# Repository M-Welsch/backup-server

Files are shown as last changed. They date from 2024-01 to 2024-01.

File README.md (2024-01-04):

# Backup Server (BaSe)

Your Home NAS requires you to make backups from time to time. Since you have better things to do, these will likely get forgotten or done irregulary. The Backup-Server aims on helping you out. It backs up your data on schedule and undocks the backup medium when the backup is done. This offers an unique way of data protection.

## Introduction (longer)

Like many other people (*cough* nerds) I have a home NAS that serves nextcloud and some other funny stuff. Thanks to a terrific community it became quite easy to setup such a thing. Many, many thanks to you all!
However, hosting my own server came with a serious disadvantage. I had to take care of the backups myself.

I built Backup Server to overcome this issue. It sleeps and therefore consumes very, very little current most of the times, wakes up when a backup is scheduled, docks to a hard drive, copys all the data from the nas, undocks and goes back to sleep.



## Implementation

The current verion is built around a banana pi mk1. It connects to the hard drive via a motor-driven pluggable sata-connection, which is the core of the whole thing. This way, the harddrive is only connected to anything if needed.

```mermaid
graph LR
A(Power Up)-->B(Dock external HDD)-->C(Conduct Backup)-->D(Schedule Next Backup)-->E(Undock external HDD)-->F(Schedule next Backup)-->G(Power Down)
```

# Components

the next hardware version shall be more flexible compared to our custom fit to the banana pi.
# base-pcu

This has the directories

- ChibiOS
- ChibiOS-Contrib

as submodules.

```shell
git submodule add git@github.com:ChibiOS/ChibiOS.git
git submodule add git@github.com:ChibiOS/ChibiOS-Contrib.git
```

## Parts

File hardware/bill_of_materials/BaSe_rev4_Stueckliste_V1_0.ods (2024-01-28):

Stückliste BaSe HW rev4
Stand: 01/28/2024
Position | Bezeichnung | Menge | Einzelpreis | Gesamtpreis | Link
100 | Raspberry Pi 4 (oder kompatibler SBC) | 1 |  | 0,00 €
200 | BaSe_PWR_V4_0 Leiterplatte | 1 | 1,63 € | 1,63 €
201 | BaSe_PWR_V4_0 Bauteile | 1 | 40,83 € | 40,83 € | 35,47 € bei 25 Stück
210 | BaSe_HMI_V1_1 Leiterplatte | 0.2 | 6,30 € | 1,26 €
211 | BaSe_HMI_V1_1 Bauteile | 1 | 4,77 € | 4,77 € | 3,67 € bei 25 Stück, 2,93€ bei 100 Stück
212 | Display Modul | 0.2 | 10,49 € | 2,10 € | https://www.amazon.de/AZDelivery-HD44780-Display-Zeichen-Arduino/dp/B08216LXVQ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
220 | BaSe_USB_Adapter_Carriage_V1_0 Leiterplatte | 1 | 0,47 € | 0,47 €
221 | BaSe_USB_Adapter_Carriage_V1_0 Bauteile | 1 |  | 0,00 € | Preis in BaSe_PWR_4_0 enthalten
230 | BaSe_USB_Adapter_Frame_V1_0 Leiterplatte | 1 | 1,63 € | 1,63 €
231 | BaSe_USB_Adapter_Frame_V1_0 Bauteile | 1 |  | 0,00 € | Preis in BaSe_PWR_4_0 enthalten
300 | BaSe_hw4_frame_v2.stl | 1 |  | 0,00 €
301 | BaSe_hw4_carriage_v1.stl | 1 |  | 0,00 €
303 | USB 2.0 A auf Micro USB | 1 |  | 0,00 €
304 | USB 3.0 A auf Micro USB 3.0 | 1 | 6,05 € | 6,05 € | https://www.ebay.de/itm/145108187455
305 | Kugellager 608 ZZ 8x22x7mm Miniaturkugellager | 2 |  | 0,00 €
400 | Mikro Getriebemotor N20 12V 60rpm | 1 |  | 0,00 € | https://www.ebay.de/itm/384457943327
401 | Gewindekupplungen | 0.2 | 7,99 € | 1,60 € | https://www.amazon.de/YOTINO-Wellenkupplungen-Schrittmotor-Koppler-Aluminiumlegierung-Gelenkverbinder/dp/B07D9JWNFC
402 | Gewindestange (10cm) + Gewindemutter | 0.2 | 13,69 € | 2,74 € | https://www.amazon.de/Mavis-Laven-Gewindestange-Trapezgewindestange-Messingmutter-300mm/dp/B07SK6YZCM
 |  |  | Summe | 63,06 €

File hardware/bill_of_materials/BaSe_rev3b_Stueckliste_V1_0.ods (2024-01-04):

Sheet: Einkaufsliste
Stückliste BaSe HW rev3b
Stand: 30.08.2020
Position | Bezeichnung | Menge | Einzelpreis | Gesamtpreis | Link
100 | BananaPi Mk1 | 1 | 38,01 € | 38,01 € | https://www.conrad.de/de/p/banana-pi-bpi-m1-banana-pi-bpi-m1-1-gb-2-x-1-0-ghz-1196100.html
200 | BaSe_PWR_V3_2 Leiterplatte | 0,2 | 11,30 € | 2,26 €
201 | BaSe_PWR_V3_2 Bauteile | 1 | 45,79 € | 45,79 € | 35,47 € bei 25 Stück
202 | Schrittmotor Treibermodul | 0,2 | 7,99 € | 1,60 € | https://www.amazon.de/ARCELI-kompatibles-Stepper-StepStick-Motortauchermodul-K%C3%BChlk%C3%B6rper-3D-Drucker-Controller-Rampen/dp/B07MY2SWQ5
203 | Micro-USB Stecker | 0,05 | 9,39 € | 0,47 € | https://www.amazon.de/gp/product/B013FJKC28/ref=ppx_yo_dt_b_asin_title_o04_s00?ie=UTF8
210 | BaSe_HMI_V1_1 Leiterplatte | 0,2 | 6,30 € | 1,26 €
211 | BaSe_HMI_V1_1 Bauteile | 1 | 4,77 € | 4,77 € | 3,67 € bei 25 Stück, 2,93€ bei 100 Stück
212 | Display Modul | 0,2 | 10,49 € | 2,10 € | https://www.amazon.de/AZDelivery-HD44780-Display-Zeichen-Arduino/dp/B08216LXVQ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
220 | BaSe_SATA_Adapter_Carriage_V1_1 Leiterplatte | 0,2 | 3,00 € | 0,60 €
221 | BaSe_SATA_Adapter_Carriage_V1_1 Bauteile | 1 | 5,89 € | 5,89 € | 5,61 € bei 25 Stück, 4,60 € bei 100 Stück
230 | BaSe_SATA_Adapter_HDD_V1_1 Leiterplatte | 0,2 | 5,00 € | 1,00 €
231 | BaSe_SATA_Adapter_HDD_V1_1 Bauteile | 1 | 10,39 € | 10,39 € | 9,07 € bei 25 Stück, 8,22 € bei 100 Stück
300 | BaSe_Auflager_Platinen_rev3.stl
301 | BaSe_Bodenplatte_rev3.stl
302 | BaSe_BP_HDD_rev1.stl
303 | BaSe_HMI_Display_Abstandsrahmen_rev1.stl
304 | BaSe_rev1_Spannlager_Gegenstueck_2020_07_19.stl
305 | BaSe_Schlitten_rev3_2020_07_19.stl
400 | Schrittmotor: Nema 17 | 1 | 7,99 € | 7,99 € | https://www.ebay.de/itm/Schrittmotor-Nema-17-Stepper-Motor-32Ncm-1-2A-42x34mm-4-wire-1m-Cable-3D-Drucker/392587286914
401 | Gewindekupplungen | 0,2 | 7,99 € | 1,60 € | https://www.amazon.de/YOTINO-Wellenkupplungen-Schrittmotor-Koppler-Aluminiumlegierung-Gelenkverbinder/dp/B07D9JWNFC
402 | Gewindestange (10cm) | 0,2 | 13,69 € | 2,74 € | https://www.amazon.de/Mavis-Laven-Gewindestange-Trapezgewindestange-Messingmutter-300mm/dp/B07SK6YZCM
403 | Linearführung + Gleitlager + Spannbacken | 0,5 | 13,49 € | 6,75 € | https://www.ebay.de/itm/2-X-400mm-8mm-Linearfuhrung-Gleitschiene-Welle-4-X-SBR20UU-Linearblock/373092586135
404 | Endschalter (KW4-3Z-3 Schnappsch gs) | 0,4 | 4,09 € | 1,64 € | https://www.ebay.de/itm/5pcs-Mikro-Endschalter-lange-Hebel-Arm-Subminiatur-KW4-3Z-3-Schnappsch-gs/163894137501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
 |  |  | Summe | 134,84 €

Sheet: BaSe_PWR_V3_2_Stueckliste
Refs | Value | Footprint | Quantity | MFR | MPN | SPR | SPN
C1;C16;C6;C7 | 100nF | Capacitor_SMD:C_0603_1608Metric_Pad1.05x0.95mm_HandSolder | 4 | - | - | - | 399-7845-1-ND
C9 | 10nF | Capacitor_SMD:C_0603_1608Metric_Pad1.05x0.95mm_HandSolder | 1 | - | - | - | 311-1572-1-ND
C24 | 1nF | Capacitor_SMD:C_0603_1608Metric_Pad1.05x0.95mm_HandSolder | 1 | - | - | - | 311-1080-1-ND
C2;C3;C10;C8;C13;C20;C17 | 1µF | Capacitor_SMD:C_0805_2012Metric_Pad1.15x1.40mm_HandSolder | 7 | - | - | Digikey | 732-7672-1-ND
C11;C4 | 100µF | Capacitor_SMD:C_1210_3225Metric_Pad1.42x2.65mm_HandSolder | 2 | - | - | - | 587-1387-1-ND
C5;C18;C15 | 10µF | Capacitor_SMD:C_1210_3225Metric_Pad1.42x2.65mm_HandSolder | 3 | - | - | - | 1276-1150-1-ND
C12 | 47nF | Capacitor_SMD:C_1210_3225Metric_Pad1.42x2.65mm_HandSolder | 1 | - | - | Digikey | 1276-1150-1-ND
C19;C14 | 220µF | Capacitor_SMD:C_Elec_6.3x7.7 | 2 | - | - | - | PCE4537CT-ND
J6 | B4B-PH-K-S(LF)(SN) | Connector_JST:JST_PH_B4B-PH-K_1x04_P2.00mm_Vertical | 1 | JST Sales America Inc. | B4B-PH-K-S(LF)(SN) | Digikey | 455-1706-ND
J4 | B9B-PH-K-S(LF)(SN) | Connector_JST:JST_PH_B9B-PH-K_1x09_P2.00mm_Vertical | 1 | JST Sales America Inc. | - | Digikey | 455-1711-ND
J2 | BPi Supply | Connector_JST:JST_XH_S2B-XH-A_1x02_P2.50mm_Horizontal | 1 | JST | - | Digikey | 455-2257-ND
D3 | 824501121 | Diode_SMD:D_SMA | 1 | - | - | Digikey | 732-9949-1-ND
D4;D5 | NO | Diode_SMD:D_SMA | 2 | - | - | - | -
D6 | NO | Diode_SMD:D_SMC | 1 | - | - | - | SK64L-TPMSCT-ND
D2;D1 | 1N4148 | Diode_SMD:D_SOD-123F | 2 | - | - | - | 1N4148WRHGCT-ND
F1 | Fuse | Fuse:Fuse_Littelfuse-NANO2-451_453 | 1 | - | - | - | F3147CT-ND
SCT1 | A4988_Module | G7_Custom:A4988_Module | 1 | - | - | - | -
FFC_Cable1 | 151670333 | G7_Custom:BOM_ITEM | 1 | - | 151670333 | Digikey | WM16429-ND
Cable_HDD_ENDSW_preconfected2 | ASPHSPH24K152 | G7_Custom:BOM_ITEM | 1 | - | ASPHSPH24K152 | Digikey | 455-3082-ND
Cable_Stepper_preconfected1;Cable_Stepper_preconfected2;Cable_Stepper_preconfected3;Cable_Stepper_preconfected4 | ASPHSPH24K51‎ | G7_Custom:BOM_ITEM | 4 | - | - | Digikey | ‎455-3081-ND‎
Cable_BPi_SPLY_preconfected2;Cable_BPi_SPLY_preconfected1 | ASXHSXH22K51 | G7_Custom:BOM_ITEM | 2 | - | - | Digikey | 455-3239-ND
Conn_Socket_Stepper1 | PHR-4 | G7_Custom:BOM_ITEM | 1 | - | - | Digikey | 455-1164-ND
Conn_Socket_at_Stepper1 | PHR-6 | G7_Custom:BOM_ITEM | 1 | - | - | Digikey | 455-1162-ND
Conn_Socket_PWR_HDD1 | PHR-9 | G7_Custom:BOM_ITEM | 1 | - | PHR-9 | Digikey | 455-1159-ND
Conn_Socket_BPi_SPLY_atJ5;Conn_Socket_BPi_SPLY1 | XHP-2 | G7_Custom:BOM_ITEM | 2 | - | - | Digikey | 455-2266-ND
M1 | BananaPi_M1 | G7_Custom:BananaPi-M1 | 1 | - | - | Digikey | SAM1212-13-ND
J1 | 12V Power In | G7_Custom:BarrelJack_Wuerth_6941xx301002 | 1 | - | - | Digikey | CP-102A-ND
FL1;FL2 | CM2021Y330R-10 | G7_Custom:CMC_Laird_CM2021Y330R-10 | 2 | - | - | - | 240-2502-1-ND
J5 | Molex 0522071860 | G7_Custom:Conn_FFC_Molex_52207-1860 | 1 | - | - | - | WM10954CT-ND
J3 | DebugAtTiny | G7_Custom:JST_XH_B4B-XH-AM_1x04_P2.50mm_Vertical | 1 | - | - | Digikey | 455-2237-ND
U2 | LMZ12003 | G7_Custom:LMZ12003_Handsolder | 1 | - | - | - | LMZ12003TZ-ADJ/NOPBCT-ND
U4 | LTC4359-MS8 | G7_Custom:MSOP-8_3x3mm_P0.65mm_Py0.45mm | 1 | Linear Technology/Analog Devices | LTC4359CMS8#TRPBF‎ | Digikey | LTC4359CMS8#TRPBFCT-ND‎
K1 | EC2-12TNU | G7_Custom:Relay_Kemet_EC2-12TNU | 1 | KEMET | EC2-12TNU | Digikey | 399-11031-5-ND
PCB1 | BaSe_PWR_V3_2 | G7_Labels:BaSe_PWR_V3_2 | 1 | - | - | - | -
FB3;FB4;FB5;FB6;FB7;FB10 | 742792602 | Inductor_SMD:L_0603_1608Metric_Pad1.05x0.95mm_HandSolder | 6 | - | - | Digikey | 732-4660-1-ND
FB2 | 742792093 | Inductor_SMD:L_0805_2012Metric_Pad1.15x1.40mm_HandSolder | 1 | - | - | Digikey | 732-1609-1-ND
H1;H2;H3;H4 | MountingHole | MountingHole:MountingHole_2.2mm_M2 | 4 | - | - | - | -
U5 | ATtiny816-S | Package_SO:SOIC-20W_7.5x12.8mm_P1.27mm | 1 | Microchip Technology | ATTINY816-SFR | Digikey | ATTINY816-SFRCT-ND
U3 | ADG734 | Package_SO:TSSOP-20_4.4x6.5mm_P0.65mm | 1 | - | - | - | ADG734BRUZ-REEL7CT-ND
Q2;Q6;Q7 | BSS123 | Package_TO_SOT_SMD:SOT-23 | 3 | - | - | - | BSS123LT1GOSCT-ND
U7 | AP2204K-3.3 | Package_TO_SOT_SMD:SOT-23-5_HandSoldering | 1 | - | - | Digikey | AP2204K-3.3TRG1DICT-ND
U1 | INA212 | Package_TO_SOT_SMD:SOT-363_SC-70-6_Handsoldering | 1 | Texas Instruments | ‎INA212AIDCKT‎ | Digikey | 296-23586-1-ND
Q3 | BSC028N06LS3 | Package_TO_SOT_SMD:TDSON-8-1 | 1 | Infineon Technologies | ‎BSC028N06NSATMA1‎ | Digikey | BSC028N06NSATMA1CT-ND‎
Q4 | BSC093N04LS | Package_TO_SOT_SMD:TDSON-8-1 | 1 | - | - | - | BSC093N04LSGATMA1CT-ND
Q1;Q5 | BS170 | Package_TO_SOT_THT:TO-92_Inline | 2 | - | - | - | BS170-D75ZCT-ND
R13;R23 | 0 | Resistor_SMD:R_0603_1608Metric_Pad1.05x0.95mm_HandSolder | 2 | - | - | - | 311-47KGRCT-ND
FB9 | 0R | Resistor_SMD:R_0603_1608Metric_Pad1.05x0.95mm_HandSolder | 1 | - | - | - | 311-47KGRCT-ND
Rfbb1 | 1,87K | Resistor_SMD:R_0603_1608Metric_Pad1.05x0.95mm_HandSolder | 1 | - | - | - | P20001CT-ND
Rfbt1;R5;R19 | 10k | Resistor_SMD:R_0603_1608Metric_Pad1.05x0.95mm_HandSolder | 3 | - | - | - | 311-10.0KHRCT-ND
R3 | 1k | Resistor_SMD:R_0603_1608Metric_Pad1.05x0.95mm_HandSolder | 1 | - | - | - | 311-1.00KHRCT-ND
R24;R6;2k4 | 1k2 | Resistor_SMD:R_0603_1608Metric_Pad1.05x0.95mm_HandSolder | 3 | - | - | - | A129689CT-ND
R8;R11;R10;R9;R12;R2;Ron1;R15;R14;R17;2k3;R20;R4;R16;R25 | 47k | Resistor_SMD:R_0603_1608Metric_Pad1.05x0.95mm_HandSolder | 15 | - | - | - | 311-47KGRCT-ND
R7;R22;R21;R18;R26;R27 | NO | Resistor_SMD:R_0603_1608Metric_Pad1.05x0.95mm_HandSolder | 6 | - | - | - | 311-47KGRCT-ND
R1 | 1m | Resistor_SMD:R_1206_3216Metric_Pad1.42x1.75mm_HandSolder | 1 | Riedon | CSR1206-0R001F1 | Digikey | 696-1369-1-ND

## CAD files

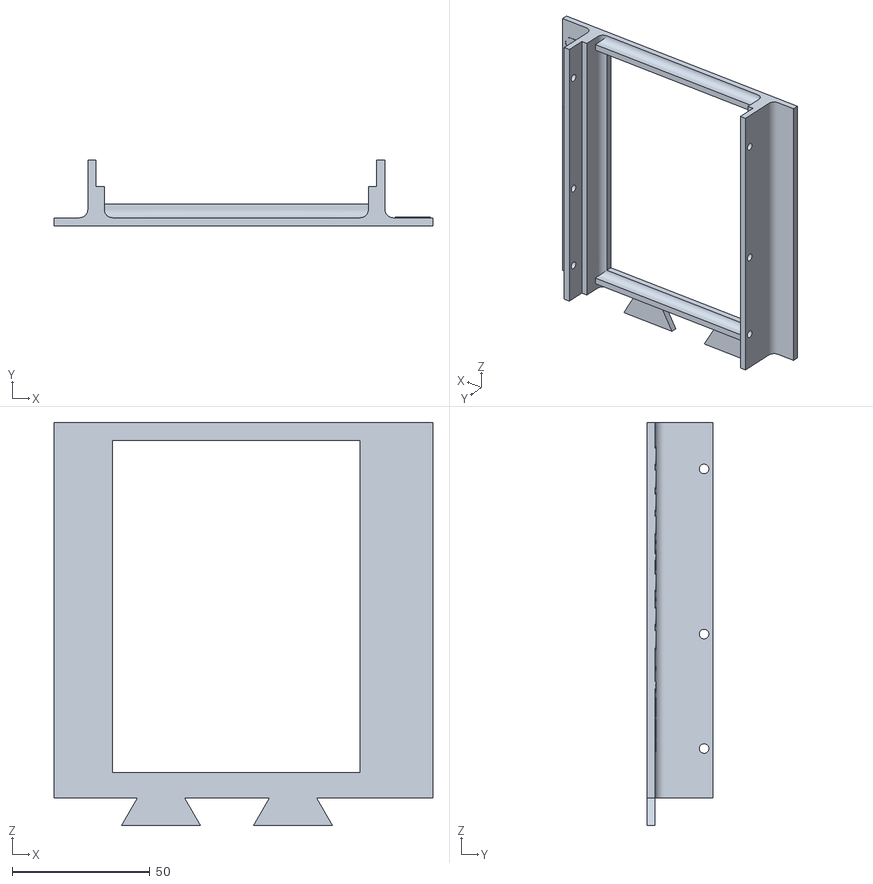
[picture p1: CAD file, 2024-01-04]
3d_printing_parts/BaSe_BP_HDD_rev1.stl
137.7 x 24.0 x 146.5

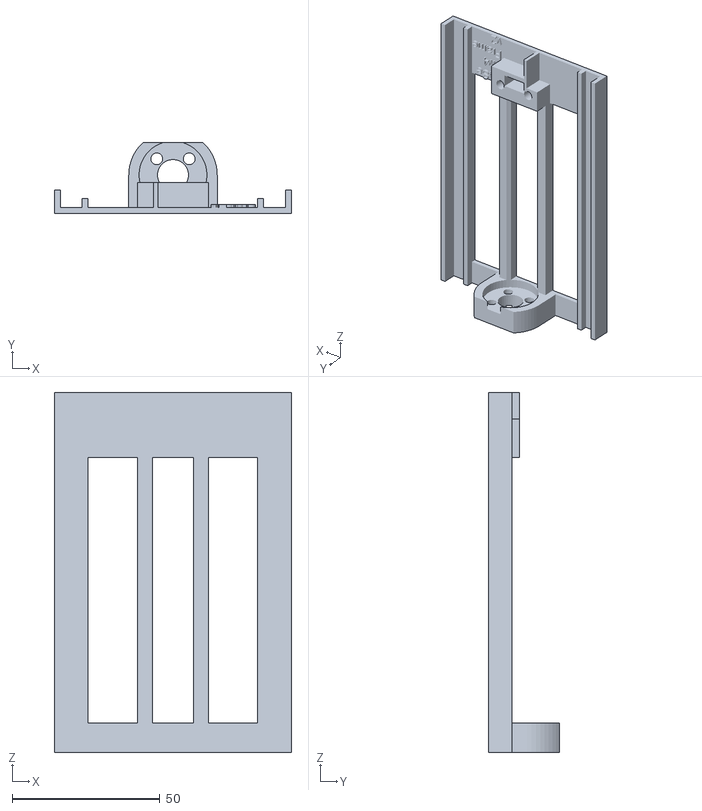
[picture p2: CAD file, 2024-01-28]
hardware/3d_printing_parts/BaSe_hw4_frame_v2.stl
80.4 x 24.0 x 122.0

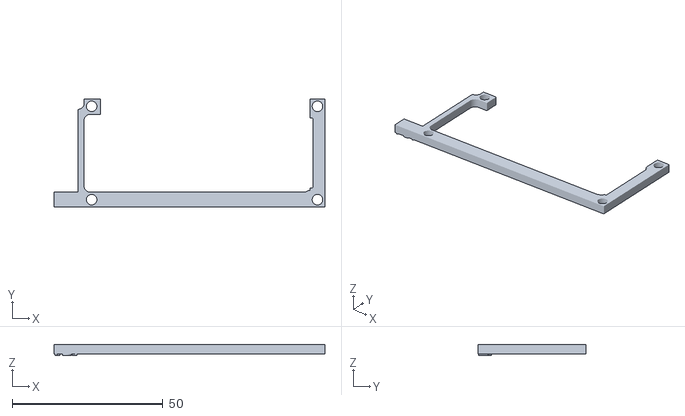
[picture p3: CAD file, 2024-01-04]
3d_printing_parts/BaSe_HMI_Display_Abstandsrahmen_rev1.stl
90.0 x 36.0 x 3.50

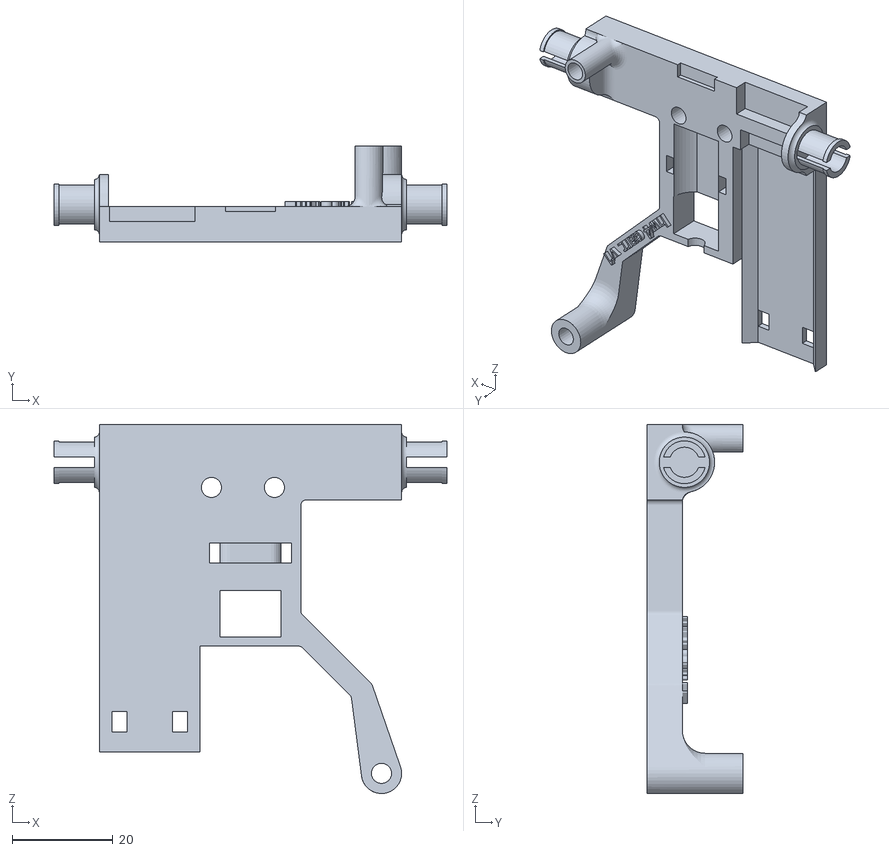
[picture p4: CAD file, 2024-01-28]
hardware/3d_printing_parts/BaSe_hw4_carriage_v1.stl
78.0 x 19.0 x 73.2

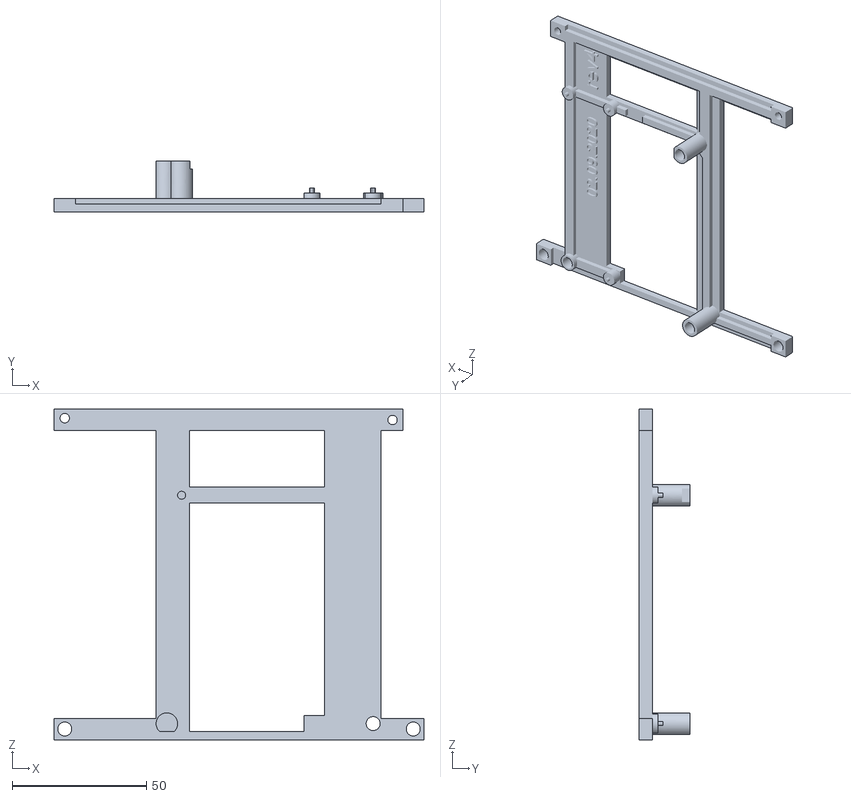
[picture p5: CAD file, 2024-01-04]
3d_printing_parts/BaSe_Auflager_Platinen_rev4.stl
137.7 x 19.0 x 123.0

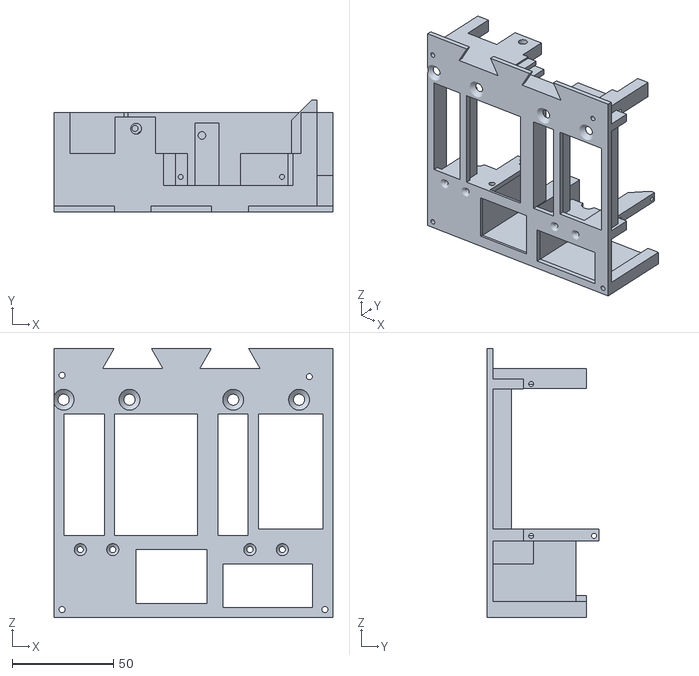
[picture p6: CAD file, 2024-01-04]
3d_printing_parts/BaSe_Bodenplatte_rev3.stl
137.7 x 55.3 x 133.0

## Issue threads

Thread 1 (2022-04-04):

use usb-connection for mechanism

M-Welsch, 2022-04-04:
# USB-C

- Plug: https://www.digikey.de/de/products/detail/jae-electronics/DX07P024MJ1R1500/5604379
  - 10.000 mating cycles
  - 5A current rating, 48V voltage rating
  - CAD models: https://www.snapeda.com/parts/DX07P024MJ1R1500/JAE%20Electronics/view-part/?ref=digikey
- Socket: take any ..

would be nice to wire VBUS to 12V and put a buck converter on the secondary side to generate the 5V.

M-Welsch, 2023-07-06:
implemented in hw rev4

Closed 2023-07-06.

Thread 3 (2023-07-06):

BaSe Websocket-Protokoll / API (WIP)

MaximilianStaab, 2023-07-06:
## Meta
### Generelles Format der JSON-Nachrichten
```json
{"topic": <String>, "data": {<String>: <Any>, ...}}
```
`"data"` ist optional.

### Erläuterungen zur Auflistung
##### Typ
- Command: Kommando vom Client zum Server (erwartet Acknowledgement)
- Query: Anfrage vom Client zum Server (erwartet Response)
- Response: Antwort vom Server zum Client (erwartet nichts)
- Push: Nachricht vom Server zum Client (erwartet nichts)

## Auflistung der Nachrichten Nachrichten
##### Shutdown-Timer pausieren
Typ: Command
```json
{"topic": "pause_shutdown_timer"}
```

##### Shutdown-Timer fortsetzen
Typ: Command
```json
{"topic": "resume_shutdown_timer"}
```

##### Shutdown-Timer Ist-Wert
Typ: Push
```json
{"topic": "shutdown_timer_state", "data": {"seconds": <int>}}
```

##### Shutdown-Befehl
Typ: Command
```json
{"topic": "shutdown_now"}
```

… to be discussed and continued.

M-Welsch, 2023-07-18:
why is the topic of a response sometimes the same as the topic of the query without the get

```
Query
{"topic": "get_log_file_list"}
Response
{"topic": "log_file_list", "data": {"file_names": [<str>, ...]}
```

and sometimes some other string like this?

```
Query
{"topic": "get_led_brightness"}
Response
{"topic": "current_led_brightness", "data": {"value": <float>}}
```

M-Welsch, 2023-07-18:
@MaximilianStaab schau bitte, welche Config-Werte noch fehlen:
https://github.com/M-Welsch/base-bcu/tree/master/base/config

jackyscript, 2023-07-22:
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
Verlinken auf https://datatracker.ietf.org/doc/html/rfc3339 ?
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

Das reicht

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

Man könnte auch nur "minutes" ab 0 Uhr übergeben? Die Stunden lassen sich ja wiederum daraus berechnen.

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

Angabe von time bzw. Referenz zu ISO 8601 zentral an einer Stelle definieren? Abweichungen sollten natürlich an der entsprechenden Stelle erwähnt werden.

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

Könnte das eine Senke sein, sicherheitstechnisch?

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

Ich sehe mail_address im Schema nicht, ist das eine <str>-Instanz im receivers-Array?

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

Wird eine Validierung am Client durchgeführt? Was ist wenn ein undefinierter Wert ungeachtet dessen übertragen wird z. B. "3"? Wird dann der maximale Wert am Server eingestellt, d. h. "1" der Command ignoriert?

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

Ich denke es sollte nur verlinkt werden und kein Inhalt aus den Logfiles angezeigt werden bzw. auf die Person verwiesen werden, die in die Logfiles einsehen kann. Wenn jemand auf die webapp unauthorisiert zugreifen sollte, wäre so ein Einblick in die Logfiles suboptimal.

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

Das bedeutet die letzten fünf Einträge werden angezeigt

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

file_name im Response ist nicht notwendig? Enthält die Query ja bereits den Namen. Was passiert im Fehlerfall, falls die Datei bspw. nicht mehr existiert, weil Anzeige in der webapp veraltet?

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

jackyscript, 2023-07-25:
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

Wir sollten überlegen, ob wir zukünftig für jede Person die Logs aus dem Server im Client anzeigen. Stattdessen den Log-Viewer nur für "authorisierte" Benutzer bereitstellen und leserliche Fehlermeldungen an den Client übergeben. Somit ein Mapping haben zwischen Exceptions und Fehlermeldungen im Client. Fehler und Exceptions werden immer auf Serverseite geloggt, aber möglichst nicht an den Client gegeben werden.
"Normale Benutzer" können fast immer mit technischen Exceptions/Fehlermeldungen etwas anfangen, "unauthorisierte" wiederum sollen möglichst nichts über das zugrundeliegende System erfahren bspw. Betriebssystem, existierende Pfade und Benutzer etc.

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

Auf Serverseite können Skripts angelegt werden. Über die Schnittstelle soll nur die Auswahl bereitgestellt werden also z. B. Pre-Backup-Hook-Scripts 1 bis 10 mit Bezeichnungen/Titel. Das Gleiche für Post-Backup-Hook-Scripts.

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

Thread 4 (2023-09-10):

BaSe PCU-Protokoll / API (WIP)

M-Welsch, 2023-09-10:
@MaximilianStaab, please transfer from yed

MaximilianStaab, 2023-09-12:
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

M-Welsch, 2023-09-12:
as implemented in https://github.com/M-Welsch/base-pcu/commit/1bcf86ef7c2da93b7d4f2d11f121926b35f2a567

```mermaid
graph LR

failed[return commandname failed]
success[return commandname succesul]
true[return true]
false[return false]

av[returns analog value]
probe-->echo[return echo]
input-->get
get-->analog
analog-->imotor_prot-->av
analog-->stator_supply_sense-->av
analog-->vin12_meas-->av
get-->digital
digital-->endswitch
endswitch-->true
endswitch-->false
digital-->docked
docked-->true
docked-->false
get-->dockingstate
get-->date

input-->set
set-->date

input-->cmd
cmd-->dock
dock-->failed
dock-->success
cmd-->undock
undock-->failed
undock-->success
cmd-->power
power-->hdd
hdd-->on
on-->failed
on-->success
hdd-->off
off-->failed
off-->success
power-->bcu
bcu-->on
bcu-->off

```

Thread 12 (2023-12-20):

directory for upcoming backup is created

M-Welsch, 2023-12-20:
# Description
we want a directory for the upcoming backup (aka the one that is being done during the current run) so we can place our increment in there

# What happens if we don't do it (aka Why is it important)?
our new backup overwrites the old one

# Definition of Ready
- [ ] as in #11, we know how the folder-structure and the naming convention looks

# Key Tasks
- [ ] compose a name for the upcoming backup
- [ ] create a directory in the right folder with this name

# Acceptance Criteria
- [ ] a correctly named (see above) folder is created when we call the corresponding function

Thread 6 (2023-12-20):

udev rule for BackupHDD is created

M-Welsch, 2023-12-20:
# Description
We want a **udev rule** so we can mount the BackupHDD by typing `mount BackupHDD`

# What happens if we don't do it (aka Why is it important)?
We would have to determine ourselves under which devicenode (like `/dev/sdxY`) the backuphdd registers. Linux provides udev which we can utilize

# Definition of Ready
we know how to fingerprint our backup drive

# Key Tasks
- [x] create a file like `/etc/udev/rules.d/99-backupserver.rules` with content like (CAREFUL: EXAMPLE!!)
```
ACTION=="add", SUBSYSTEM=="block", ATTRS{idVendor}=="0951", ATTRS{idProduct}=="1666", SYMLINK+="BASE_USB_STICK"
```

# Acceptance Criteria
- [x] the backup drive appears as `/dev/BACKUPHDD` when it is connected and powered

Closed 2024-01-04.

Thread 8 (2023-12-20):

Communication with PCU works

M-Welsch, 2023-12-20:
# Description
We want a way to communicate with the PCU to control the hardware periphery and the wakeup feature

# What happens if we don't do it (aka Why is it important)?
- We cannot dock, power therefore access the hard drive
- We cannot wake the BCU after sleep

# Definition of Ready
PCU exposes a virtual serial port

# Key Tasks
Write functions that transfer commands over the serial port to the PCU
- [x] dock, undock
- [x] power, unpower
- [x] set current time
- [x] set wakeup time
- [x] power off the bcu

# Acceptance Criteria
- [x] when we call these functions, the PCU docks and powers.
- [x] when we set any of these times, it can be read back correctly
- [x] when we set a wakeup time, the supply for the BCU comes back on at the expected time
- [x] when we send the command to power off, we still have enough time to shut down linux before the supply relay opens

M-Welsch, 2024-01-04:
cannot tell if the time before power cutoff is long enough because we cannot execute the "shutdown -h now" command yet

M-Welsch, 2024-01-16:
Test
- had a stopwatch
- executed `sudo shutdown -h now` and started the stopwatch
- stopped when power cunsumption decreased significantly (from 300 to around 100mA at 12V)
was aronund 5s

Changed default waiting time from 5 to 10s

Closed 2024-01-16.

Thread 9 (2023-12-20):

systemd file is in place

M-Welsch, 2023-12-20:
# Description
We want a systemd (`*.service`) file so our base-application (the python program here) starts up when the SBC is powered.

# What happens if we don't do it (aka Why is it important)?
The python program doesn't run, SBC will idle forever

# Definition of Ready
we know where the base-application is located

# Key Tasks
- [x] create a file like (`/etc/systemd/system/base-application.service`)

# Acceptance Criteria
- [x] when we power on the BCU, the base-application gets started

Closed 2024-01-09.

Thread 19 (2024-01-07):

get rid of rsync errors `/media/Backup... no such file or directory`

M-Welsch, 2024-01-07:
# Description
During #15 we saw issues that probably relate to the mounting process

```
Jan 07 21:10:04 raspberrypi python3[707]: mount: /media/BackupHDD: must be superuser to use mount.
...
Jan 07 21:10:04 raspberrypi python3[318]: 2024-01-07 21:10:04,460 INFO: __main__: Fehlerausgabe: rsync: [Receiver] mkdir "/media/BackupHDD/backups/current" failed: No such file or directory (2)
Jan 07 21:10:04 raspberrypi python3[318]: rsync error: error in file IO (code 11) at main.c(787) [Receiver=3.2.3]
```

The steps the program does usually work. In case they don't, they work when entered manually to the terminal. Maybe a timing problem

# What happens if we don't do it (aka Why is it important)?
a backup will sometimes fail. About 1/4 of the times

# Definition of Ready
- [x] no prequisites

# Key Tasks
- [x] implement a way to make sure the hdd is ready. Have some timeout so it doesn't get stuck forever
- [x] create automated test that verifies this doesn't happen

# Acceptance Criteria
- [x] we don't get such a log as above in 100 runs

M-Welsch, 2024-01-08:
see this logfile for more info: [logfile.log](https://github.com/M-Welsch/backup-server/files/13866070/logfile.log)

M-Welsch, 2024-01-08:
verification

```python
    docking_trials = 2
    while not await pcu.cmd.dock():
        docking_trials -= 1
        if not docking_trials:
            raise RuntimeError("cannot dock")
```

M-Welsch, 2024-01-08:
longer test that updates the testfiles on nas on startup of the backupserver
```
[Unit]
Description=Generate fresh testfiles on NAS for Backup Server

[Service]
User=base
Group=base
Type=simple
ExecStart=/usr/bin/bash /home/base/backup-server/software/utils/generate_testdata_on_nas.sh

[Install]
WantedBy=multi-user.target
```

should run over night

M-Welsch, 2024-01-08:
Suggestion: implement handshake when PCU communication is established. This way we can make sure that this "ominous first command fail" happens controlled during the init phase and not during operation at some random point of time

M-Welsch, 2024-01-09:
After 29 runs the program stopped because it needed 2 trials and ran into timeout
the warning appeared 22 times

Closed 2024-01-10.

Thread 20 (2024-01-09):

pcu handshake

M-Welsch, 2024-01-09:
# Description

as a fix for #19:

- the pcu sometimes doesn't respond to the very first command after the connection has physically established (like one of the devices has powered up)
- all subsequent commands run flawlessly to current knowledge
- therefore we want a handshake process at initialization of pcu that makes sure these "ominous first command fail" happens controlled during the init phase and not during operation at some random point of time

# What happens if we don't do it (aka Why is it important)?

the first message to the pcu (whatever that is) might fail. Therefore a catch would have to be implemented in several commands

# Definition of Ready
no prequisites

# Key Tasks
- [x] decide for a command to use for this kind of "probe"
- [x] implement into the pcu code
- [x] integrate into the backupserver process

# Acceptance Criteria
- [x] the warning that docking fails for the first time appears significantly less often. Like only every 20th time

Closed 2024-01-10.

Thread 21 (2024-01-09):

date readback from pcu can fail

M-Welsch, 2024-01-09:
# Description

log tail from `journalctl -u base`

```
Jan 09 09:26:58 raspberrypi python3[1489]: 2024-01-09 09:26:58,773 INFO: __main__: Programming PCU. Setting current time and time for next wakeup
Jan 09 09:27:01 raspberrypi python3[1489]: 2024-01-09 09:27:01,822 DEBUG: __main__: read current time from pcu: 2024-09-01 09:38:50
Jan 09 09:27:04 raspberrypi python3[1489]: Traceback (most recent call last):
Jan 09 09:27:04 raspberrypi python3[1489]:   File "/usr/lib/python3.9/runpy.py", line 197, in _run_module_as_main
Jan 09 09:27:04 raspberrypi python3[1489]:     return _run_code(code, main_globals, None,
Jan 09 09:27:04 raspberrypi python3[1489]:   File "/usr/lib/python3.9/runpy.py", line 87, in _run_code
Jan 09 09:27:04 raspberrypi python3[1489]:     exec(code, run_globals)
Jan 09 09:27:04 raspberrypi python3[1489]:   File "/home/base/backup-server/software/bcu/__main__.py", line 135, in <module>
Jan 09 09:27:04 raspberrypi python3[1489]:     asyncio.run(main())
Jan 09 09:27:04 raspberrypi python3[1489]:   File "/usr/lib/python3.9/asyncio/runners.py", line 44, in run
Jan 09 09:27:04 raspberrypi python3[1489]:     return loop.run_until_complete(main)
Jan 09 09:27:04 raspberrypi python3[1489]:   File "/usr/lib/python3.9/asyncio/base_events.py", line 642, in run_until_complete
Jan 09 09:27:04 raspberrypi python3[1489]:     return future.result()
Jan 09 09:27:04 raspberrypi python3[1489]:   File "/home/base/backup-server/software/bcu/__main__.py", line 129, in main
Jan 09 09:27:04 raspberrypi python3[1489]:     await set_wakeup_time()
Jan 09 09:27:04 raspberrypi python3[1489]:   File "/home/base/backup-server/software/bcu/__main__.py", line 108, in set_wakeup_time
Jan 09 09:27:04 raspberrypi python3[1489]:     LOG.debug(f"read wakeup time from pcu: {await pcu.get.date.wakeup()}")
Jan 09 09:27:04 raspberrypi python3[1489]:   File "/home/base/backup-server/software/bcu/pcu.py", line 103, in wakeup
Jan 09 09:27:04 raspberrypi python3[1489]:     return await _get_date(date_kind=DateKind.wakeup)
Jan 09 09:27:04 raspberrypi python3[1489]:   File "/home/base/backup-server/software/bcu/pcu.py", line 324, in _get_date
Jan 09 09:27:04 raspberrypi python3[1489]:     return _pcu_timestring_to_datetime(datestr)
Jan 09 09:27:04 raspberrypi python3[1489]:   File "/home/base/backup-server/software/bcu/pcu.py", line 313, in _pcu_timestring_to_datetime
Jan 09 09:27:04 raspberrypi python3[1489]:     return datetime.strptime(pcu_output, "%H:%M:%S - %d-%m-%Y")
Jan 09 09:27:04 raspberrypi python3[1489]:   File "/usr/lib/python3.9/_strptime.py", line 568, in _strptime_datetime
Jan 09 09:27:04 raspberrypi python3[1489]:     tt, fraction, gmtoff_fraction = _strptime(data_string, format)
Jan 09 09:27:04 raspberrypi python3[1489]:   File "/usr/lib/python3.9/_strptime.py", line 349, in _strptime
Jan 09 09:27:04 raspberrypi python3[1489]:     raise ValueError("time data %r does not match format %r" %
Jan 09 09:27:04 raspberrypi python3[1489]: ValueError: time data '08:33:00 - 00-09-1980' does not match format '%H:%M:%S - %d-%m-%Y'
```

`08:33:00 - 00-09-1980` is wrong in multiple ways

- why is month 0?
- why is the date in the 1980 range?

# What happens if we don't do it (aka Why is it important)?

it currently prevents the system to continue

# Definition of Ready
no prequisites

# Key Tasks
- [x] decide on a strategy like "log and ignore" or "fix". Decided for "log and ignore"
- [x] implement

# Acceptance Criteria
- [ ] this date readback doesn't prevent the system from running

M-Welsch, 2024-01-09:
implement a catch and retry for this and test again

M-Welsch, 2024-01-09:
was probably due to the shell being misconfigured after I checked out

53643eacb36c25e24c037f8a507f167dc9bea332

Closed 2024-01-09.

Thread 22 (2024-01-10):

basic CI

M-Welsch, 2024-01-10:
# Description

We want a way to make sure the Backup Server does its job in an automated way. One way that I can think of is having a "system in the loop" test that basically does the following
- a python script in the test-folder that imports our high-level backup-server python module. no, this cannot verify the shutdown

- a set of testfiles on the nas that is accessible over rsync daemon (size, folder structure and stuff has to be decided on)
- a test backup server that is connected to an external drive (preferably a USB 3 hard drive to be most realistic)
- a python script that runs on a computer
  - listens to the serial debug terminal of the PCU to verify it undergoes the correct steps
  - listens to the bcu (over ssh?) and verifies it undergoes the correct steps
  - compares the data on the nas and the base and does a verification
- (optional, but cool) put it all on another raspberry pi or some other computer, so this can all run on the side
- (optional, but very cool) implement a github action that runs this test automatically every push or so

# What happens if we don't do it (aka Why is it important)?

We wouldn't have an automated test that can verify that our product works as intended. The consequences are the necessity to verify stuff manually or take the risk of having more bugs than necessary.

# Definition of Ready
- [ ] #19
- [ ] #15

# Key Tasks
- [ ] print necessary messages on serial debug console of the PCU
- [ ]

# Acceptance Criteria
- [ ]

M-Welsch, 2024-01-12:
I added a file `testmode` inside the bcu directory that switches the rsync source from backup-data-source to backup-testdata-source

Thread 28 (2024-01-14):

Starting up without network connection leaves HDD engaged

M-Welsch, 2024-01-14:
# Description

What I observed

- powered up
- forgot to attach network cable
- base docked
- and stayed like that. Probably the program crashed when trying to do some network stuff, gotta check journalctl

# What happens if we don't do it (aka Why is it important)?

if network isn't available for some reason, hdd is always docked
- exposed
- consumes excess power

# Definition of Ready
no prequisites

# Key Tasks
- [ ] check journalctl what the issue is
- [ ] catch that and default to undock and shutdown
- [ ] maybe check network beforehand and don't even dock i.e. when NAS isn't reachable

# Acceptance Criteria
- [ ] when I remove the network cable and start up base, it either doesn't dock to begin with or undocks shortly after docking

M-Welsch, 2024-01-15:
journalctl -u backupserver
```
Jan 14 17:47:46 raspberrypi python3[320]: 2024-01-14 17:47:46,045 DEBUG: __main__: obtained IP Address of NAS: 192.168.0.2
Jan 14 17:47:46 raspberrypi python3[320]: 2024-01-14 17:47:46,047 DEBUG: __main__: Backing up with command rsync -aH --stats --delete 192.168.0.2::backup_testdata_source/* /me>
Jan 14 17:47:46 raspberrypi python3[320]: 2024-01-14 17:47:46,069 INFO: __main__: Starting Backup...
Jan 14 17:47:49 raspberrypi python3[320]: 2024-01-14 17:47:49,239 INFO: __main__: Backup finished.
Jan 14 17:47:49 raspberrypi python3[320]: 2024-01-14 17:47:49,240 DEBUG: __main__: Backup output task finished.
Jan 14 17:47:49 raspberrypi python3[320]: 2024-01-14 17:47:49,241 ERROR: __main__: Fehlerausgabe: rsync: [Receiver] failed to connect to 192.168.0.2 (192.168.0.2): No route to>
Jan 14 17:47:49 raspberrypi python3[320]: rsync error: error in socket IO (code 10) at clientserver.c(137) [Receiver=3.2.3]
```

M-Welsch, 2024-01-16:
just removed the line that tracked #19. It killed the program on purpose on any rsync fault to leave base in the respective state

Closed 2024-01-16.

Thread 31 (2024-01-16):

[END OF MVP] reallife backup test

M-Welsch, 2024-01-16:
# Description
conduct a real backup

# What happens if we don't do it (aka Why is it important)?
we want to close the mvp and thereby have a minimally working product that we can put aside without having bad feelings. This serves then as a basis for future improvements

# Definition of Ready
- [x] have the raspi 4
- [x] have a usb-sata bridge
- [x] have a hardlink-copy from the latest existing backup on the hard drive

# Key Tasks
- [x] put the software on the raspi 4
- [x] configure it all (linux stuff)
- [x] set wait-time between backups to 12h for
- [x] power it on
- [x] let it run for 3 days
- [x] check if backup is integer
- [x] check logs

# Acceptance Criteria
- [x] backup ran sucessfully

M-Welsch, 2024-01-20:
currently blocked by #33

M-Welsch, 2024-01-20:
blocked by

```
Jan 20 23:00:04 basehw4sn2 python3[1523]: 2024-01-20 23:00:04,429 DEBUG: __main__: Mounting HDD...
Jan 20 23:00:04 basehw4sn2 python3[1528]: mount: /media/BackupHDD: must be superuser to use mount.
Jan 20 23:00:04 basehw4sn2 python3[1528]:        dmesg(1) may have more information after failed mount system call.
Jan 20 23:00:04 basehw4sn2 python3[1531]: Pseudo-terminal will not be allocated because stdin is not a terminal.
Jan 20 23:00:04 basehw4sn2 python3[1523]: 2024-01-20 23:00:04,459 DEBUG: __main__: obtained IP Address of NAS: 192.168.0.2
Jan 20 23:00:04 basehw4sn2 python3[1523]: 2024-01-20 23:00:04,459 DEBUG: __main__: Backing up with command rsync -aH --stats --delete 192.168.0.2::backup_data_source/* /media/BackupHDD/backups/current
Jan 20 23:00:04 basehw4sn2 python3[1523]: 2024-01-20 23:00:04,463 INFO: __main__: Starting Backup...
Jan 20 23:00:04 basehw4sn2 python3[1523]: 2024-01-20 23:00:04,579 INFO: __main__: Backup finished.
Jan 20 23:00:04 basehw4sn2 python3[1523]: 2024-01-20 23:00:04,579 DEBUG: __main__: Backup output task finished.
Jan 20 23:00:04 basehw4sn2 python3[1523]: 2024-01-20 23:00:04,579 ERROR: __main__: Fehlerausgabe: rsync: [Receiver] mkdir "/media/BackupHDD/backups/current" failed: No such file or directory (2)
Jan 20 23:00:04 basehw4sn2 python3[1523]: rsync error: error in file IO (code 11) at main.c(791) [Receiver=3.2.7]
Jan 20 23:00:04 basehw4sn2 python3[1523]: 2024-01-20 23:00:04,579 INFO: __main__: Disconnecting Backup HDD
```

have to investigate

M-Welsch, 2024-01-21:
turned out that https://github.com/M-Welsch/backup-server/blob/63b6059b673297c73210776ea0d5ae5afd555763/software/bcu/__main__.py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 would have to change to (using `shell=True`), but I don't know why

```
        subprocess.call("mount /dev/BACKUPHDD", shell=True)  # Todo: why do I have to use the shell here??
```

M-Welsch, 2024-01-21:
First run. Logs are not of particular importance, just to have them somewhere around

```
Jan 21 11:02:38 basehw4sn2 python3[1068]: 2024-01-21 11:02:38,148 INFO: __main__: Connect Backup HDD
Jan 21 11:02:38 basehw4sn2 python3[1068]: 2024-01-21 11:02:38,149 DEBUG: __main__: Docking...
Jan 21 11:02:41 basehw4sn2 python3[1068]: 2024-01-21 11:02:41,167 WARNING: __main__: couldn't dock, try another time.
Jan 21 11:02:44 basehw4sn2 python3[1068]: 2024-01-21 11:02:44,190 DEBUG: __main__: Switching HDD power on...
Jan 21 11:02:55 basehw4sn2 python3[1068]: 2024-01-21 11:02:55,707 DEBUG: __main__: Mounting HDD...
Jan 21 11:02:55 basehw4sn2 python3[1077]: mount: /media/BackupHDD: must be superuser to use mount.
Jan 21 11:02:55 basehw4sn2 python3[1077]:        dmesg(1) may have more information after failed mount system call.
Jan 21 11:03:00 basehw4sn2 python3[1068]: 2024-01-21 11:03:00,728 WARNING: __main__: mounting of backupHDD failed, try another time
Jan 21 11:03:06 basehw4sn2 python3[1098]: Pseudo-terminal will not be allocated because stdin is not a terminal.
Jan 21 11:03:06 basehw4sn2 python3[1068]: 2024-01-21 11:03:06,035 DEBUG: __main__: obtained IP Address of NAS: 192.168.0.2
Jan 21 11:03:06 basehw4sn2 python3[1068]: 2024-01-21 11:03:06,035 DEBUG: __main__: Backing up with command rsync -aH --stats --delete 192.168.0.2::backup_data_source/* /media/BackupHDD/backups/current
Jan 21 11:03:06 basehw4sn2 python3[1068]: 2024-01-21 11:03:06,040 INFO: __main__: Starting Backup...
Jan 21 11:05:02 basehw4sn2 python3[1068]: 2024-01-21 11:05:02,909 DEBUG: __main__: Live Output: skipping non-regular file "dietpi_userdata/docker-data/overlay2/21af8d916fe354465a7de2b90c82064466943a566bb354763458a2cf8bfd0b8e-init/work/work/#45"
Jan 21 11:05:44 basehw4sn2 python3[1068]: 2024-01-21 11:05:44,215 DEBUG: __main__: Live Output: skipping non-regular file "dietpi_userdata/docker-data/overlay2/3c42bedd10eb9960b5bca04cb761ed20f18fd3b349374b1182d4d447f93e250c-init/work/work/#14"
Jan 21 11:07:06 basehw4sn2 python3[1068]: 2024-01-21 11:07:06,823 DEBUG: __main__: Live Output: skipping non-regular file "dietpi_userdata/docker-data/overlay2/42f0d5d6dce71c39c53cea3a5f09ade87ac7e88ff980e2311879da5f654509f5-init/work/work/#22"
Jan 21 11:07:13 basehw4sn2 python3[1068]: 2024-01-21 11:07:13,091 DEBUG: __main__: Live Output: skipping non-regular file "dietpi_userdata/docker-data/overlay2/57a3c63b8a8139710205d2dc1225a9e031fcfdc51f4c5aac4339d062c75d7255/diff/usr/src/arm-alignment.patch"
Jan 21 11:07:13 basehw4sn2 python3[1068]: 2024-01-21 11:07:13,092 DEBUG: __main__: Live Output: skipping non-regular file "dietpi_userdata/docker-data/overlay2/57a3c63b8a8139710205d2dc1225a9e031fcfdc51f4c5aac4339d062c75d7255/diff/usr/src/asynctio_unix_events.patch"
Jan 21 11:07:13 basehw4sn2 python3[1068]: 2024-01-21 11:07:13,092 DEBUG: __main__: Live Output: skipping non-regular file "dietpi_userdata/docker-data/overlay2/57a3c63b8a8139710205d2dc1225a9e031fcfdc51f4c5aac4339d062c75d7255/diff/usr/src/fix-xattrs-glibc.patch"
Jan 21 11:07:13 basehw4sn2 python3[1068]: 2024-01-21 11:07:13,092 DEBUG: __main__: Live Output: skipping non-regular file "dietpi_userdata/docker-data/overlay2/57a3c63b8a8139710205d2dc1225a9e031fcfdc51f4c5aac4339d062c75d7255/diff/usr/src/musl-find_library.patch"
Jan 21 11:07:25 basehw4sn2 python3[1068]: 2024-01-21 11:07:25,149 DEBUG: __main__: Live Output: skipping non-regular file "dietpi_userdata/docker-data/overlay2/6231f558106aff6b98f6a10f102e45d9b06ef7690e065d08c48baf6fbd8be424/diff/usr/src/requirements.txt"
Jan 21 11:07:26 basehw4sn2 python3[1068]: 2024-01-21 11:07:26,451 DEBUG: __main__: Live Output: skipping non-regular file "dietpi_userdata/docker-data/overlay2/75c11afb9bcbaf1965bee540af40c9b49061dbcbe33869fee3b96d59470d3eb0-init/work/work/#41"
Jan 21 11:07:27 basehw4sn2 python3[1068]: 2024-01-21 11:07:27,833 DEBUG: __main__: Live Output: skipping non-regular file "dietpi_userdata/docker-data/overlay2/7ecca733b5cce3eb5fa22ca6aa5769e89930091426dcbf6673daac83a7142b6d-init/work/work/#4f"
Jan 21 11:07:39 basehw4sn2 python3[1068]: 2024-01-21 11:07:39,246 DEBUG: __main__: Live Output: skipping non-regular file "dietpi_userdata/docker-data/overlay2/7ecca733b5cce3eb5fa22ca6aa5769e89930091426dcbf6673daac83a7142b6d/work/work/#1c"
Jan 21 11:07:49 basehw4sn2 python3[1068]: 2024-01-21 11:07:49,606 DEBUG: __main__: Live Output: skipping non-regular file "dietpi_userdata/docker-data/overlay2/9b0cd1b17f2f3f8808c72add8512440f43736952e819c37805ddaf412db02f74/diff/usr/src/telldus-fix-gcc-11-issues.patch"
Jan 21 11:07:50 basehw4sn2 python3[1068]: 2024-01-21 11:07:50,910 DEBUG: __main__: Live Output: skipping non-regular file "dietpi_userdata/docker-data/overlay2/a09b99a2a0020d22034f41e2743690d1da12760dbef0465e55224355970565d4-init/work/work/#5b"
Jan 21 11:08:08 basehw4sn2 python3[1068]: 2024-01-21 11:08:08,345 DEBUG: __main__: Live Output: skipping non-regular file "dietpi_userdata/docker-data/overlay2/d0402d66df200c9e9acc18de08261cf1cf43eea0acfdd73c60b5046cb595993d/diff/usr/src/libcec-fix-null-return.patch"
Jan 21 11:08:11 basehw4sn2 python3[1068]: 2024-01-21 11:08:11,938 DEBUG: __main__: Live Output: skipping non-regular file "dietpi_userdata/docker-data/overlay2/e38fd4115d660a4ddc201c59327a72a5c403597937d9c3043a027ccc5b143b41-init/work/work/#4b8"
Jan 21 11:08:24 basehw4sn2 python3[1068]: 2024-01-21 11:08:24,366 DEBUG: __main__: Live Output: skipping non-regular file "dietpi_userdata/docker-data/volumes/backingFsBlockDev"
Jan 21 11:50:37 basehw4sn2 python3[1068]: 2024-01-21 11:50:37,420 DEBUG: __main__: Live Output:
Jan 21 11:50:37 basehw4sn2 python3[1068]: 2024-01-21 11:50:37,433 DEBUG: __main__: Live Output: Number of files: 1,975,449 (reg: 1,666,118, dir: 293,388, link: 15,923, special: 20)
Jan 21 11:50:37 basehw4sn2 python3[1068]: 2024-01-21 11:50:37,433 DEBUG: __main__: Live Output: Number of created files: 85,862 (reg: 71,320, dir: 13,270, link: 1,270, special: 2)
Jan 21 11:50:37 basehw4sn2 python3[1068]: 2024-01-21 11:50:37,436 DEBUG: __main__: Live Output: Number of deleted files: 5,181 (reg: 4,468, dir: 713)
Jan 21 11:50:37 basehw4sn2 python3[1068]: 2024-01-21 11:50:37,436 DEBUG: __main__: Live Output: Number of regular files transferred: 71,168
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
M-Welsch, 2024-01-22:
modified rsync command. Removed the * after the source. (source: https://stackoverflow.com/a/35452860). Tested it beforehand. Operation looks the same

```shell
rsync -aH --stats --delete 192.168.0.2::backup_data_source/* /media/BackupHDD/backups/current
# to
rsync -aH --stats --delete 192.168.0.2::backup_data_source/ /media/BackupHDD/backups/current
```

M-Welsch, 2024-01-22:
next logs:

```
Jan 22 21:12:11 basehw4sn2 python3[985]: 2024-01-22 21:12:11,672 WARNING: __main__: Live Output: ERROR: hdd0/nextcloud_old/martha/files/Bilder/2021_04_23_HedwigOmaZuBesuch/DSC_8486.JPG failed verification -- update discarded.
Jan 22 21:22:51 basehw4sn2 python3[985]: 2024-01-22 21:22:51,194 WARNING: __main__: Live Output: rsync: [sender] read errors mapping "/hdd0/share/MundM/Bilder/2020/2020_10_03-04_Annas_erster_Geburtstag/DSCN5181.JPG" (in backup_data_source): Input/output error (5)
Jan 22 21:23:22 basehw4sn2 python3[985]: 2024-01-22 21:23:22,803 WARNING: __main__: Live Output: rsync: [sender] read errors mapping "/hdd0/share/MundM/Bilder/2020/2020_10_03-04_Annas_erster_Geburtstag/DSCN5181.JPG" (in backup_data_source): Input/output error (5)
Jan 22 21:23:22 basehw4sn2 python3[985]: 2024-01-22 21:23:22,813 WARNING: __main__: Live Output: ERROR: hdd0/share/MundM/Bilder/2020/2020_10_03-04_Annas_erster_Geburtstag/DSCN5181.JPG failed verification -- update discarded.
Jan 22 21:25:16 basehw4sn2 python3[985]: 2024-01-22 21:25:16,420 DEBUG: __main__: Live Output:
Jan 22 21:25:16 basehw4sn2 python3[985]: 2024-01-22 21:25:16,421 DEBUG: __main__: Live Output: Number of files: 1,964,672 (reg: 1,657,053, dir: 292,305, link: 15,296, special: 18)
Jan 22 21:25:16 basehw4sn2 python3[985]: 2024-01-22 21:25:16,422 DEBUG: __main__: Live Output: Number of created files: 13 (reg: 13)
# ... stats ...

Jan 22 21:25:16 basehw4sn2 python3[985]: 2024-01-22 21:25:16,460 WARNING: __main__: Live Output: rsync error: some files/attrs were not transferred (see previous errors) (code 23) at main.c(1865) [generator=3.2.7]
Jan 22 21:25:16 basehw4sn2 python3[985]: 2024-01-22 21:25:16,497 INFO: __main__: Backup finished.
```

here are the errors (picked out from above)

```
Jan 22 21:12:11 basehw4sn2 python3[985]: 2024-01-22 21:12:11,672 WARNING: __main__: Live Output: ERROR: hdd0/nextcloud_old/martha/files/Bilder/2021_04_23_HedwigOmaZuBesuch/DSC_8486.JPG failed verification -- update discarded.
...
Jan 22 21:23:22 basehw4sn2 python3[985]: 2024-01-22 21:23:22,813 WARNING: __main__: Live Output: ERROR: hdd0/share/MundM/Bilder/2020/2020_10_03-04_Annas_erster_Geburtstag/DSCN5181.JPG failed verification -- update discarded.
...
Jan 22 21:25:16 basehw4sn2 python3[985]: 2024-01-22 21:25:16,497 INFO: __main__: Backup finished.
```

between the errors and the finished-log are 2 and 23 minutes. Unlikely that the errors caused rsync to stop. Btw. there are no errors logged on the server side

Closed 2024-01-26.

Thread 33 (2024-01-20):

syslog message "Cannot enable. Maybe the USB cable is bad?"

M-Welsch, 2024-01-20:
# Description

when doing a backup with the raspi4 hardware, the file transfer was very slow and the syslog showed
```
Cannot enable. Maybe the USB cable is bad?
```

moreover `lsusb -t` showed the backupHDD (physically a usb 3.0 stick) was registered for 480M, which points to a USB 2 connection rather than USB 3. In this case it should have shown 5000M

# What happens if we don't do it (aka Why is it important)?

backups will be very slow. Therefore long connection times of the hdd and long uptimes for the BaSe itself. Both lead to higher risks of damage.

# Definition of Ready
no prequisites

# Key Tasks
- [ ] decide if this blocks the MVP
- [ ] connect BaSe USB 3 line to a computer and see if it shows the same error
- [ ] check with a USB 3.0 hdd
- [ ] fix the bug or create another issue

# Acceptance Criteria

either
- [ ] the message doesn't show up anymore when hdd is engaged
or
- [ ] we have another issue that handles the bugfix

M-Welsch, 2024-01-20:
Directly connected to PC it shows "5000M". Over BaSe USB line it only shows 480M. This indicates there's a hardware problem with the USB connection

M-Welsch, 2024-01-20:
There was a soldering issue.

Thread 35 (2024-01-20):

[Hardware] Cannot power HDD

M-Welsch, 2024-01-20:
# Description

when trying to power an (older) 3,5'' HDD, the HDD couldn't spin up. It kept on powercycling. This also happened when I connected it directly to the raspberry pi 4. When connecting it to the laptop, it worked.

Possible solution is to set the 5V-Voltage to 5,1V. For that I would have to replace the LM9625 fixed regulator to a adjustable one.

# What happens if we don't do it (aka Why is it important)?

We cannot put data to hard drives (or at least the hard drive I tested with)

# Definition of Ready
no prequisites

# Key Tasks
- [x] check if a higher 5V voltage like 5,1 solves the problem

# Acceptance Criteria
- [x] The HDD in question can spin up

M-Welsch, 2024-01-20:
after bridging the Ferrite in the 5V-line it worked fine

Closed 2024-01-20.

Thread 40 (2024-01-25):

[PCU] clarify what should happen if hdd is docked during startup and shutdown-request?

M-Welsch, 2024-01-25:
Two scenarios that don't cause any functional trouble but might cause some in the future.

1. HDD is docked during shutdown request. Currently the backup server would just shut down and leave the hdd undocked.
2. HDD is docked during startup. Currently we just proceed.

ad 1: it's pretty clear that it should be undocked before shutdown. However not sure if this should be reported to the BCU as an "error" and handled there or just undock

ad 2: if we make sure that hdd is docked off at shutdown, we might just leave 2 as it is.

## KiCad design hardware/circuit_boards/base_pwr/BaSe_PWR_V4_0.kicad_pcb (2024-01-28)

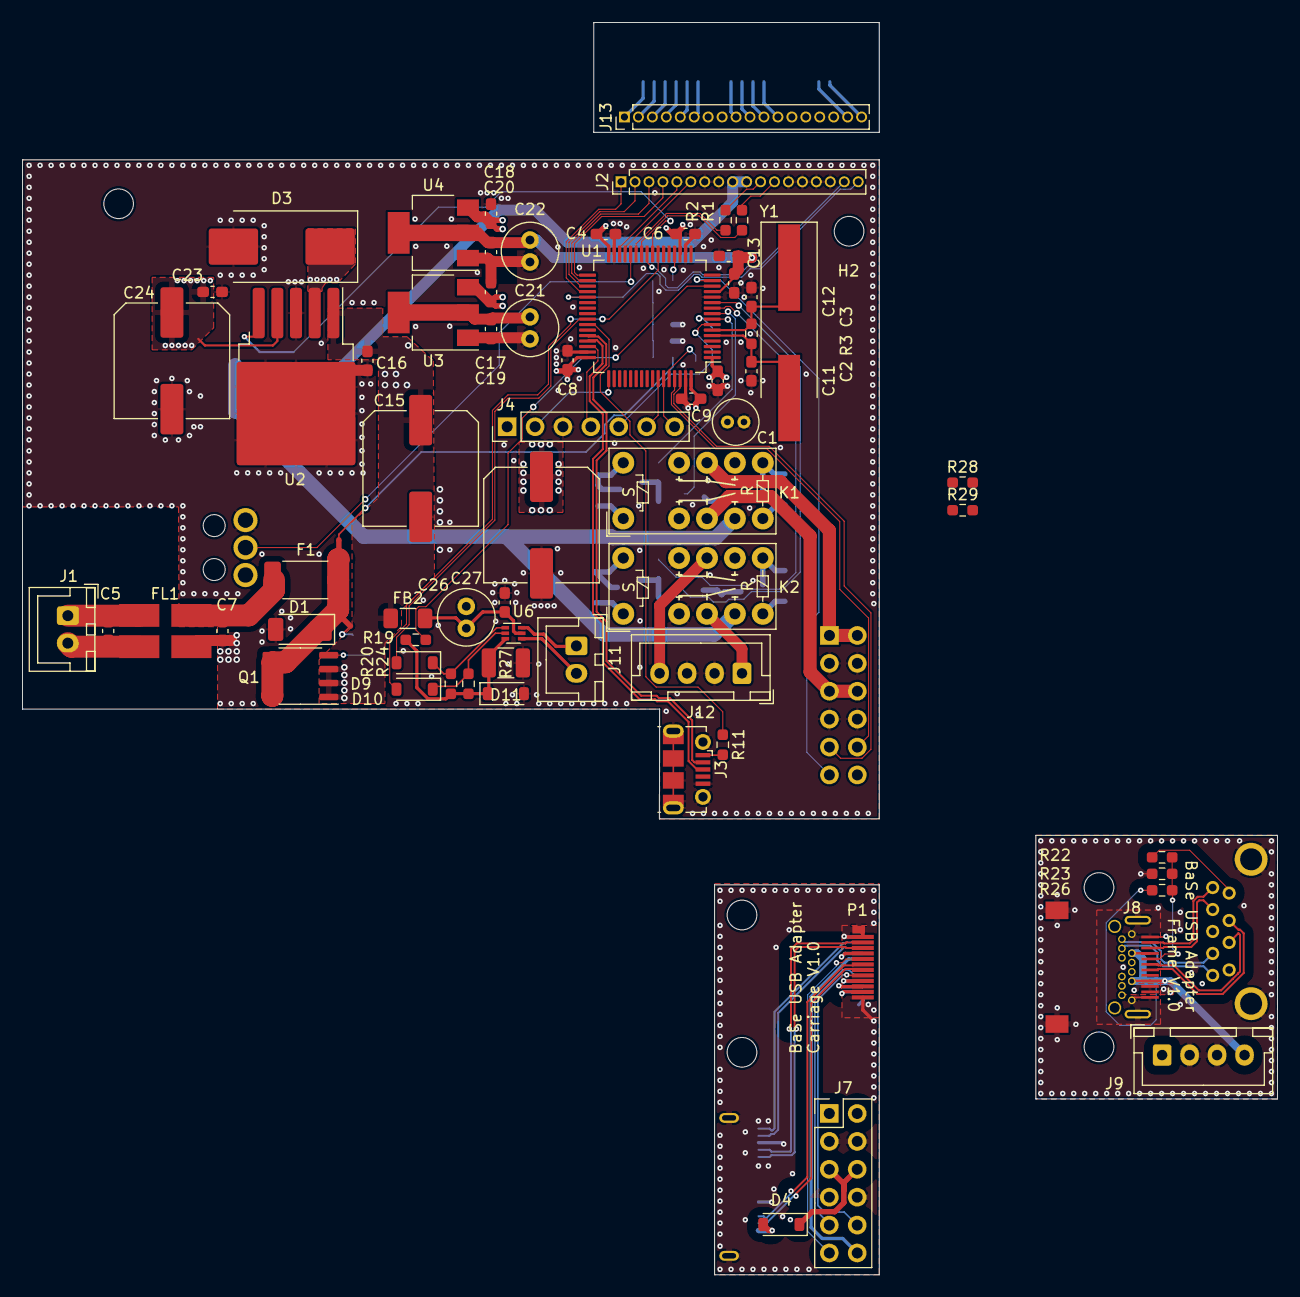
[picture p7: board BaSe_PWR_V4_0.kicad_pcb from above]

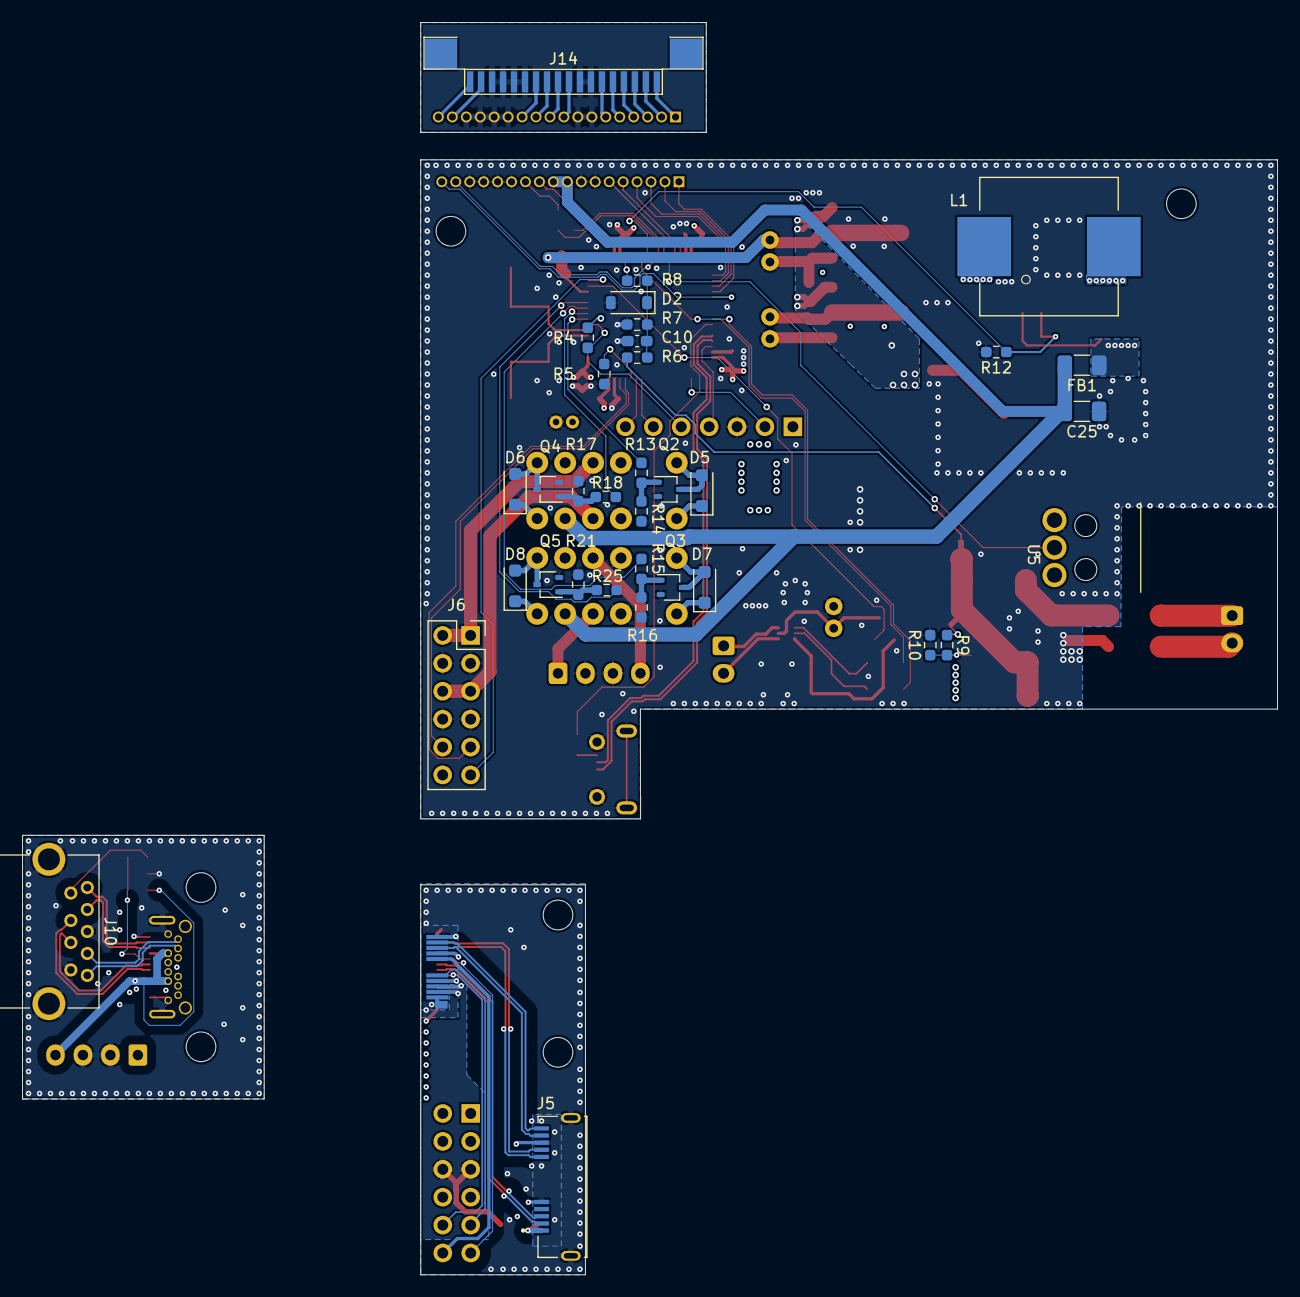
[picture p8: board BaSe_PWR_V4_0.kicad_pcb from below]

Board: 4 copper layers, 78.0 x 60.0 mm, 109 parts (34 on the bottom side), 106 nets.

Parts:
C1: 4.7µF; C_Radial_D4.0mm_H7.0mm_P1.50mm
C2, C3: 20pF; C_0603_1608Metric_Pad1.08x0.95mm_HandSolder
C4, C6, C8, C9, C10, C11, C16, C17, C18, C19, C20, C23, C27: 100nF; C_0603_1608Metric_Pad1.08x0.95mm_HandSolder
C5, C7: C_0603_1608Metric_Pad1.08x0.95mm_HandSolder
C12: 10nF; C_0603_1608Metric_Pad1.08x0.95mm_HandSolder
C13: 1µF; C_0603_1608Metric_Pad1.08x0.95mm_HandSolder
C14, C15, C24: 220µF; C_Elec_10x10.2
C21, C22, C26: 22µF; C_Radial_D5.0mm_H11.0mm_P2.00mm
C25: 10µF; C_1206_3216Metric_Pad1.33x1.80mm_HandSolder
D1: 824501121; D_SOD-128
D2, D9, D10: SD103CW-E3-08; D_SOD-123
D3: SK34-TP; D_SMC_Handsoldering
D4: SK64L-TPMSCT-ND; D_SOD-123
D5, D6, D7, D8: 1N4148WRHGCT-ND; D_SOD-123F
D11: 2.5V; D_SOD-123
F1: Fuse_2512_6332Metric_Pad1.52x3.35mm_HandSolder
FB1, FB2: FerriteBead; C_1206_3216Metric_Pad1.33x1.80mm_HandSolder
FL1: CMC_Laird_CM2021Y330R-10
H1, H2, H3, H4, H5, H6: MountingHole; MountingHole_2.7mm_M2.5_DIN965
J1: 12VDC In; JST_XH_B2B-XH-A_1x02_P2.50mm_Vertical
J2: HRS-1B-16-GA; PinHeader_1x18_P1.27mm_Vertical
J3: USB_B_Micro; USB_Micro-B_Molex-105017-0001
J4: Conn_01x07_Pin; PinHeader_1x07_P2.54mm_Vertical
J5: USB3_B_Micro; conn_usb3bmicro_GSB343K331HR
J6: Conn_02x06_Odd_Even; PinSocket_2x06_P2.54mm_Vertical
J7: Conn_02x06_Odd_Even; PinHeader_2x06_P2.54mm_Vertical
J8: USB_C_Receptacle; conn_usbc_socket_RAHPCUC31AU1TR
J9, J12: Conn_01x04_Socket; JST_XH_B4B-XH-A_1x04_P2.50mm_Vertical
J10: USB3_A; STEWARD_USB3_A_SS-52000-001
J11: MOTOR; JST_XH_B2B-XH-A_1x02_P2.50mm_Vertical
J13: HPH1-A-16-UA; PinHeader_1x18_P1.27mm_Vertical
J14: molex_fcc_05220
K1, K2: Kemet_EC2-12TNU
L1: 47µH; L_Wuerth_WE-PD-Typ-LS_Handsoldering
NT1, NT2: NetTie_2; NetTie-2_SMD_Pad0.5mm
P1: USB_C_Plug; Molex_USBC_Plug_1054440011
Q1: AOSP21321; SO-8_3.9x4.9mm_P1.27mm
Q2, Q3, Q4, Q5: BSS214NW; SOT-323_SC-70
R1, R2, R8, R10: 100; R_0603_1608Metric_Pad0.98x0.95mm_HandSolder
R3: R; R_0603_1608Metric_Pad0.98x0.95mm_HandSolder
R4, R5, R11, R20, R24, R28: 10k; R_0603_1608Metric_Pad0.98x0.95mm_HandSolder
R6, R9: 100k; R_0603_1608Metric_Pad0.98x0.95mm_HandSolder
R7: 24,9k; R_0603_1608Metric_Pad0.98x0.95mm_HandSolder
R12, R14, R16, R17, R21: 47k; R_0603_1608Metric_Pad0.98x0.95mm_HandSolder
R13, R15, R18, R19, R25: 1k; R_0603_1608Metric_Pad0.98x0.95mm_HandSolder
R22: 13,3k; R_0603_1608Metric_Pad0.98x0.95mm_HandSolder
R23: 3,16k; R_0603_1608Metric_Pad0.98x0.95mm_HandSolder
R26: 15,8k; R_0603_1608Metric_Pad0.98x0.95mm_HandSolder
R27: R; R_1210_3225Metric_Pad1.30x2.65mm_HandSolder
R29: 8,87k; R_0603_1608Metric_Pad0.98x0.95mm_HandSolder
U1: STM32F070RBTx; LQFP-64_10x10mm_P0.5mm
U2: LM2596S-5; TO-263-5_TabPin3
U3, U4: AMS1117-3.3; SOT-223-3_TabPin2
U5: TS0101F020V4
U6: DRV8220; SOT-563
Y1: 8MHz; Crystal_SMD_HC49-SD_HandSoldering

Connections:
+3.3VA: C12.1, C13.1, C20.1, C22.1, U1.13 (VDDA), U4.2 (VO)
+3V3_STBY: C1.1, C4.1, C6.1, C8.1, C9.1, C11.1, C19.1, C21.1, J4.1, J6.12, R4.2, R28.1, R29.2, U1.1 (VDD), U1.19 (VDD), U1.32 (VDD), U1.48 (VDD), U1.64 (VDD), U3.2 (VO)
+5V: C25.2, FB1.2, J2.9, J2.10, K1.5, K2.5
+5VA: J8.A10 (RX2-), J8.A11 (RX2+), J8.B2 (TX2+), J8.B3 (TX2-), J9.1, J10.1 (VBUS), R22.1
+12V: C14.1, C15.1, C16.2, C17.1, C18.1, D5.1 (K), D6.1 (K), D7.1 (K), D8.1 (K), FB2.1, K1.1, K1.6, K1.8, K2.1, K2.6, K2.8, Q1.1 (S), Q1.2 (S), Q1.3 (S), U2.1 (VIN), U3.3 (VI), U4.3 (VI)
+12VA: J8.A4 (VBUS), J8.A9 (VBUS), J8.B4 (VBUS), J8.B9 (VBUS), J9.4, R26.1
/12v_motor: C26.1, C27.1, FB2.2, U6.5 (VM)
/12vin_meas: R8.2, U1.20 (PA4)
/+5V_HDD: J6.5, J6.6, K1.4
/+5V_HDD_: D4.1 (K), J7.5, J7.6, P1.A10 (RX2-), P1.A11 (RX2+), P1.B2 (TX2+), P1.B3 (TX2-)
/+5V_sbu: J12.1, K2.4
/+5v_out: C23.2, C24.1, FB1.1, L1.2, U2.4 (FB)
/+12V_HDD: J6.1, J6.2, K1.9
/+12V_HDD_: J7.1, J7.2, P1.A4 (VBUS), P1.A9 (VBUS), P1.B4 (VBUS), P1.B9 (VBUS)
/+12V_sbu: J12.4, K2.9
/DC_IN+: C5.2, FL1.1, J1.1
/DC_IN-: C5.1, FL1.2, J1.2
/DC_prefuse: C7.1, F1.2, FL1.4
/DC_preprot: D1.1 (A1), F1.1, NT1.2, NT2.2, Q1.5 (D), Q1.6 (D), Q1.7 (D), Q1.8 (D)
/Dis_DB4: J2.4, U1.33 (PB12)
/Dis_DB5: J2.3, U1.34 (PB13)
/Dis_DB6: J2.2, U1.35 (PB14)
/Dis_DB7: J2.1, U1.36 (PB15)
/Dis_E: J2.5, U1.30 (PB11)
/Dis_PWM: J2.12, R1.2
/Dis_RS: J2.6, U1.29 (PB10)
/GND_HMI: J13.7, J13.8, J13.13, J13.14, J13.15, J13.16, J14.7, J14.8, J14.13, J14.14, J14.15, J14.16
/LED_HMI: J2.11, R2.2
/SW: D3.1 (K), L1.1, U2.2 (OUT)
/SW_HDD_Off: R18.1, U1.9 (PC1)
/SW_HDD_On: R13.1, U1.8 (PC0)
/Taster_0: J2.17, U1.25 (PC5)
/Taster_1: J2.18, U1.37 (PC6)
/USB_D+: J3.3 (D+), U1.45 (PA12)
/USB_D-: J3.2 (D-), U1.44 (PA11)
/aux_3v3: J7.12, P1.B8 (SBU2)
/aux_i2c_scl: J7.10, P1.A8 (SBU1)
/aux_i2c_sda: J7.9, P1.B5 (VCONN)
/boot0: R5.1, U1.60 (BOOT0)
/hmi_pwm0: R1.1, U1.26 (PB0)
/hmi_pwm1: R2.1, U1.27 (PB1)
/i2c1_scl: J6.10, U1.61 (PB8)
/i2c1_sda: J6.9, U1.62 (PB9)
/imotor: D11.1 (K), R19.2, R20.2, R24.2, R27.1, U6.3 (GND)
/imotor_prot: R19.1, U1.14 (PA0)
/in1: D9.1 (K), R20.1, U6.1 (IN1)
/in1_mcu: D9.2 (A), U1.41 (PA8)
/in2: D10.1 (K), R24.1, U6.2 (IN2)
/in2_mcu: D10.2 (A), U1.23 (PA7)
/l1_rx+: J8.B11 (RX1+), J10.6 (SSRX+)
/l1_rx-: J8.B10 (RX1-), J10.5 (SSRX-)
/l1_tx+: J8.A2 (TX1+), J10.9 (SSTX+)
/l1_tx-: J8.A3 (TX1-), J10.8 (SSTX-)
/lane1_d+: J8.A6 (D+), J10.3 (D+)
/lane1_d-: J8.A7 (D-), J10.2 (D-)
/motor1: J11.1, U6.6 (OUT1)
/motor2: J11.2, U6.4 (OUT2)
/stator_d+: J5.3 (D+), P1.A6 (D+)
/stator_d-: J5.2 (D-), P1.A7 (D-)
/stator_rx+: J5.10 (SSRX+), P1.B11 (RX1+)
/stator_rx-: J5.9 (SSRX-), P1.B10 (RX1-)
/stator_supply_sense: J6.11, R29.1, U1.15 (PA1)
/stator_supply_sense_: J7.11, P1.A5 (CC), R28.2
/stator_tx+: J5.7 (SSTX+), P1.A2 (TX1+)
/stator_tx-: J5.6 (SSTX-), P1.A3 (TX1-)
/supply_sense: J8.A5 (CC1), R22.2, R23.1, R26.2
/sw_sbu_off: R25.1, U1.11 (PC3)
/sw_sbu_on: R15.1, U1.10 (PC2)
/swclk: J4.2, U1.49 (PA14)
/swdio: J4.4, U1.46 (PA13)
/usart1_rx: J4.7, U1.59 (PB7)
/usart1_tx: J4.6, U1.58 (PB6)
/vbus_sense: R11.1, U1.42 (PA9)
/~LM2596S_ON: R12.1, U1.24 (PC4), U2.5 (~ON/OFF)
/~endswitch_undocked: U1.28 (PB2), U5.NO
/~rst: J4.5, R4.1, U1.7 (NRST)
GND: C1.2, C2.1, C3.1, C4.2, C6.2, C7.2, C8.2, C9.2, C10.2, C11.2, C12.2, C13.2, C14.2, C15.2, C16.1, C17.2, C18.2, C19.2, C20.2, C21.2, C22.2, C23.1, C24.2, C25.1, C26.2, C27.2, D1.2 (A2), D2.2 (A), D3.2 (A), D11.2 (A), FL1.3, J2.7, J2.8, J2.13, J2.14, J2.15, J2.16, J3.5 (GND), J3.6 (Shield), J4.3, J6.3, J6.4, J6.7, J6.8, J12.2, J12.3, K1.3, K1.10, K2.3, K2.10, Q2.2 (S), Q3.2 (S), Q4.2 (S), Q5.2 (S), R5.2, R7.1, R10.2, R12.2, R14.1, R16.1, R17.1, R21.1, R27.2, U1.12 (VSSA), U1.18 (VSS), U1.31 (VSS), U1.47 (VSS), U1.63 (VSS), U2.3 (GND), U3.1 (GND), U4.1 (GND), U5.C
GND1: J5.5 (GND), J5.8 (DRAIN), J5.11 (SHIELD), J7.3, J7.4, J7.7, J7.8, P1.A1 (GND), P1.A12 (GND), P1.B1 (GND), P1.B12 (GND), P1.S1 (SHIELD)
GND2: J8.A1 (GND), J8.A12 (GND), J8.B1 (GND), J8.B12 (GND), J8.S1 (SHIELD), J9.2, J9.3, J10.4 (GND), J10.7 (DRAIN), J10.10 (SHIELD), R23.2
unnamed: C10.1, D2.1 (K), R6.1, R7.2, R8.1
unnamed: D4.2 (A), J5.1 (VBUS)
unnamed: D5.2 (A), K1.12, Q2.3 (D)
unnamed: D6.2 (A), K1.7, Q4.3 (D)
unnamed: D7.2 (A), K2.12, Q3.3 (D)
unnamed: D8.2 (A), K2.7, Q5.3 (D)
unnamed: J3.1 (VBUS), R11.2
unnamed: J13.1, J14.1
unnamed: J13.2, J14.2
unnamed: J13.3, J14.3
unnamed: J13.4, J14.4
unnamed: J13.5, J14.5
unnamed: J13.6, J14.6
unnamed: J13.9, J13.10, J14.9, J14.10
unnamed: J13.11, J14.11
unnamed: J13.12, J14.12
unnamed: J13.17, J14.17
unnamed: J13.18, J14.18
unnamed: NT1.1, R6.2
unnamed: NT2.1, R9.1
unnamed: Q1.4 (G), R9.2, R10.1
unnamed: Q2.1 (G), R13.2, R14.2
unnamed: Q3.1 (G), R15.2, R16.2
unnamed: Q4.1 (G), R17.2, R18.2
unnamed: Q5.1 (G), R21.2, R25.2
unnamed: C2.2, R3.1, U1.5 (PF0), Y1.2
unnamed: C3.2, R3.2, U1.6 (PF1), Y1.1

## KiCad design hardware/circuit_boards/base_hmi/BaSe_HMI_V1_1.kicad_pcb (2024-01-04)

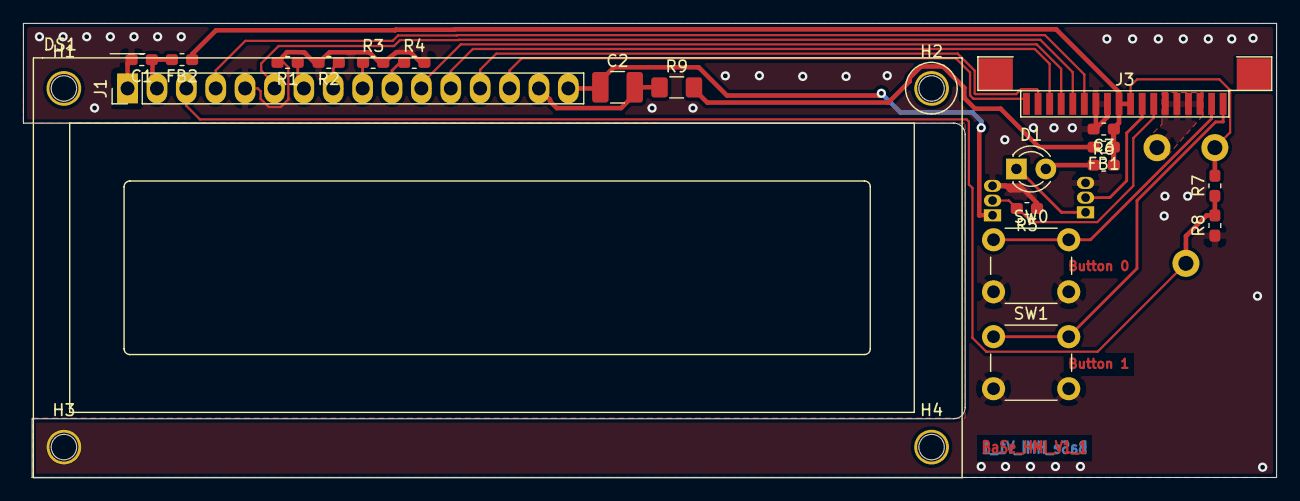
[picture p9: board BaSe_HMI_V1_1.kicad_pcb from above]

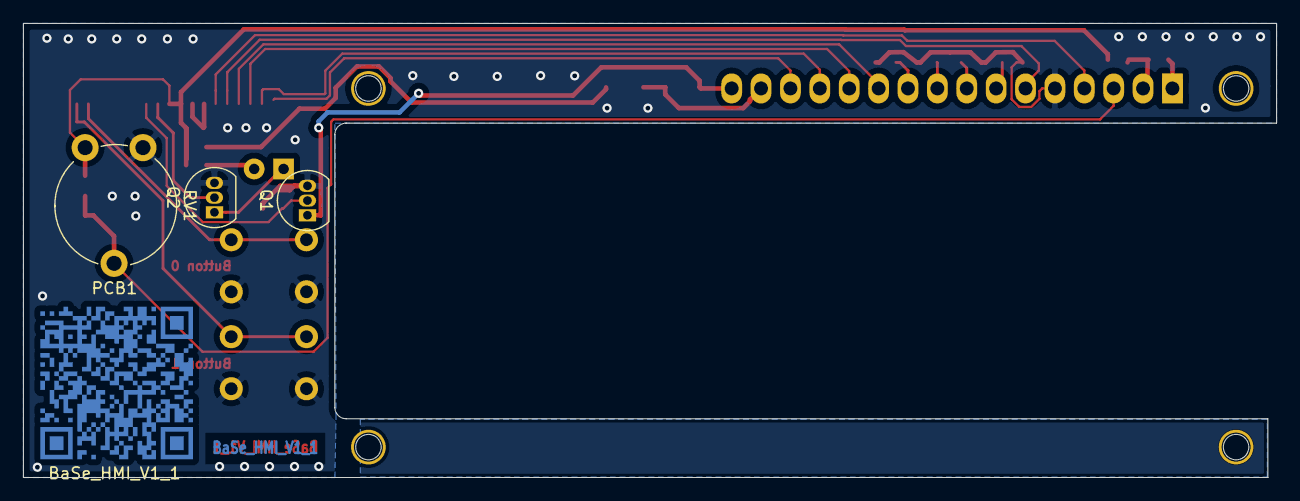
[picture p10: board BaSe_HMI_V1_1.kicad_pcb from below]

Board: 2 copper layers, 108.3 x 39.2 mm, 28 parts (4 on the bottom side), 23 nets.

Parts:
C1, C3: 100nF; C_0603_1608Metric_Pad1.05x0.95mm_HandSolder
C2: 100µF; C_1210_3225Metric_Pad1.42x2.65mm_HandSolder
D1: LED; LED_D3.0mm_9.5mm_Standoff
DS1: WC1602A; WC1602A_3.5mm_over_PCB
FB1, FB2: 742792602; L_0603_1608Metric_Pad1.05x0.95mm_HandSolder
H1, H2, H3, H4: MountingHole; MountingHole_2.2mm_M2
J1: Conn_01x16; PinHeader_1x16_P2.54mm_Vertical
J3: 0522071860; Conn_FFC_Molex_52207-1860
PCB1: BaSe_HMI_V1_1
Q1, Q2: BS170; TO-92_Inline
R1, R2, R3, R4: NO; R_0603_1608Metric_Pad1.05x0.95mm_HandSolder
R5: 10k; R_0603_1608Metric_Pad1.05x0.95mm_HandSolder
R6: 56R; R_0603_1608Metric_Pad1.05x0.95mm_HandSolder
R7: 43k; R_0603_1608Metric_Pad1.05x0.95mm_HandSolder
R8: 2k2; R_0603_1608Metric_Pad1.05x0.95mm_HandSolder
R9: 4,3R; R_1206_3216Metric_Pad1.42x1.75mm_HandSolder
RV1: R_POT; Potentiometer_Piher_PT-10-V10_Vertical
SW0, SW1: SW_Push; SW_PUSH_6mm_H7.3mm

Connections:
+5V: C3.1, FB1.1, FB2.1, J3.9, J3.10, R6.2, R7.2, RV1.1
/Dis_DB4: DS1.11, J1.11, J3.15
/Dis_DB5: DS1.12, J1.12, J3.16
/Dis_DB6: DS1.13, J1.13, J3.17
/Dis_DB7: DS1.14, J1.14, J3.18
/Dis_E: DS1.6, J3.14
/Dis_PWM: J3.7, Q1.2, R5.2
/Dis_RS: DS1.4, J3.13
/Dis_Vdd: C1.1, DS1.2, FB2.2
/LED+: C2.2, DS1.15, J1.15, R9.1
/LED-: C2.1, DS1.16, J1.16, Q1.1
/LED_HMI: J3.8, Q2.2
/Taster_0: J3.2, SW0.1
/Taster_1: J3.1, SW1.1
GND: C1.2, C3.2, DS1.1, DS1.5, J1.1, J1.5, J3.3, J3.4, J3.5, J3.6, J3.11, J3.12, Q1.3, Q2.3, R1.2, R2.2, R3.2, R4.2, R5.1, R8.1, RV1.3, SW0.2, SW1.2
unnamed: D1.1, Q2.1
unnamed: D1.2, R6.1
unnamed: DS1.3, R7.1, R8.2, RV1.2
unnamed: DS1.7, R1.1
unnamed: DS1.8, R2.1
unnamed: DS1.9, R3.1
unnamed: DS1.10, R4.1
unnamed: FB1.2, R9.2

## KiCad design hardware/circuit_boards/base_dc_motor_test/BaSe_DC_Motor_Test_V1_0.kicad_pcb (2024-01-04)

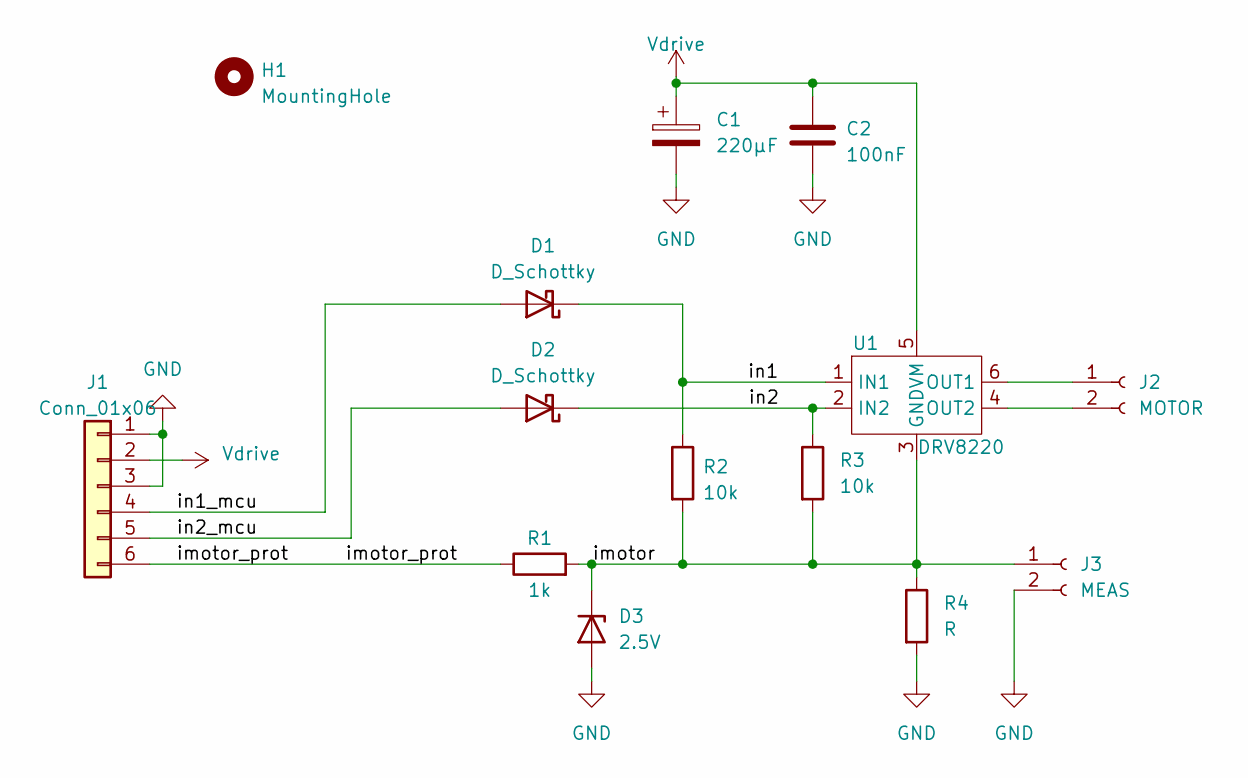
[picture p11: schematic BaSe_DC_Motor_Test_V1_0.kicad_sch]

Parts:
C1: 220µF; C_Elec_6.3x7.7
C2: 100nF; C_0603_1608Metric_Pad1.08x0.95mm_HandSolder
D1, D2: D_Schottky; D_SOD-123; MPN SD103CW-E3-08
D3: 2.5V; D_SOD-123
H1: MountingHole; MountingHole_3.2mm_M3
J1: Conn_01x06; PinHeader_1x06_P2.54mm_Vertical
J2: MOTOR; PinHeader_1x02_P2.54mm_Vertical
J3: MEAS; PinHeader_1x02_P2.54mm_Vertical
R1: 1k; R_0603_1608Metric_Pad0.98x0.95mm_HandSolder
R2, R3: 10k; R_0603_1608Metric_Pad0.98x0.95mm_HandSolder
R4: R; R_1210_3225Metric_Pad1.30x2.65mm_HandSolder
U1: DRV8220; SOT-563

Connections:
/imotor: D3.1 (K), J3.1, R1.2, R2.2, R3.2, R4.1, U1.3 (GND)
/imotor_prot: J1.6, R1.1
/in1: D1.1 (K), R2.1, U1.1 (IN1)
/in1_mcu: D1.2 (A), J1.4
/in2: D2.1 (K), R3.1, U1.2 (IN2)
/in2_mcu: D2.2 (A), J1.5
GND: C1.2, C2.2, D3.2 (A), J1.1, J1.3, J3.2, R4.2
unnamed: J2.1, U1.6 (OUT1)
unnamed: J2.2, U1.4 (OUT2)
Vdrive: C1.1, C2.1, J1.2, U1.5 (VM)

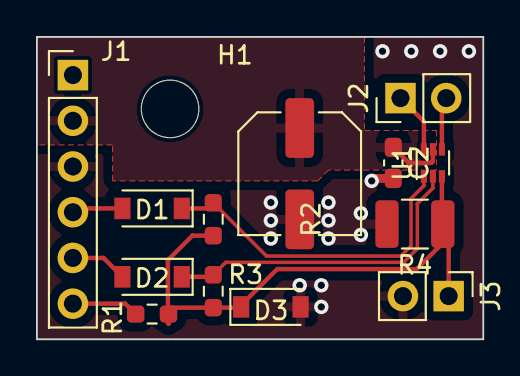
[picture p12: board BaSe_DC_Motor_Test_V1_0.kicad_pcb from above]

Board: 2 copper layers, 24.8 x 16.8 mm, 14 parts (0 on the bottom side), 10 nets.

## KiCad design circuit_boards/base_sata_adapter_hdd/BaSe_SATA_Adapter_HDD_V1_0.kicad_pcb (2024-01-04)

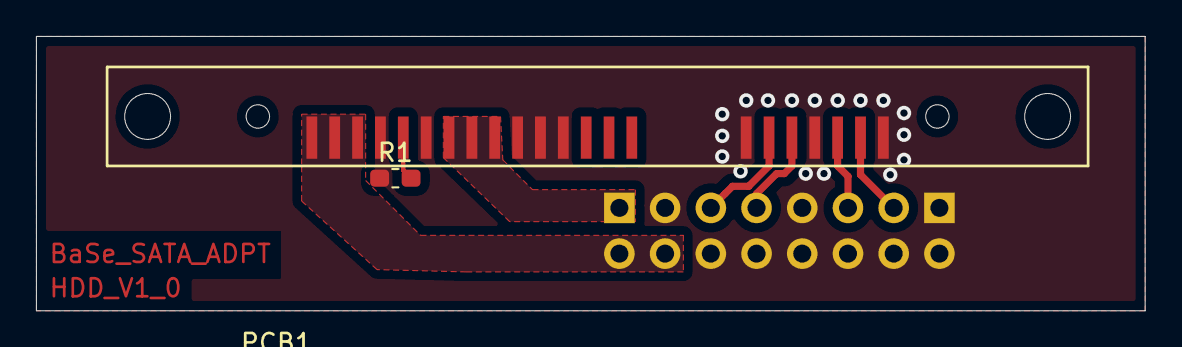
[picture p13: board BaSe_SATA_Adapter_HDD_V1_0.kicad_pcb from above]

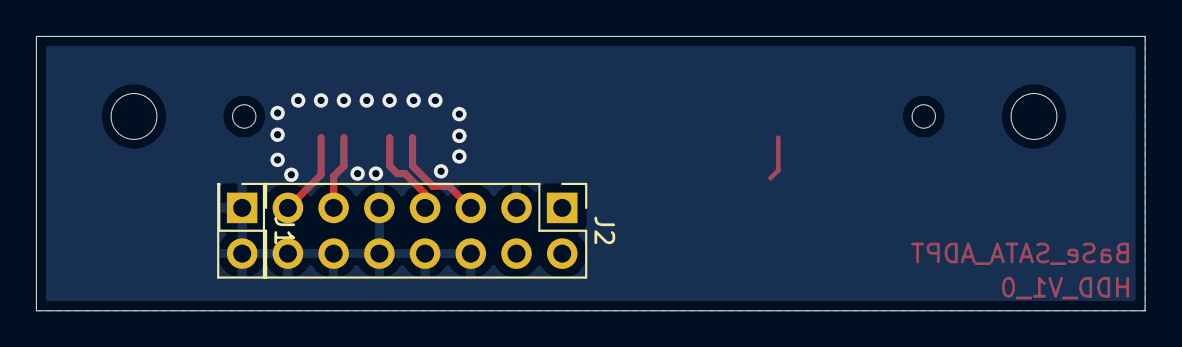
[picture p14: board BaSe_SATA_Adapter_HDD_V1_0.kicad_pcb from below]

Board: 2 copper layers, 61.6 x 15.2 mm, 5 parts (2 on the bottom side), 8 nets.

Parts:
J1: 821-22-002-10-002101; Conn_Spring_MaxMill_821-22-002-10-002101
J2: 823-22-014-10-001101; Conn_Spring_MaxMill_823-22-014-10-001101
PCB1: BaSe_SATA_Adapter_V1_0; BaSe_SATA_Adapter_HDD_V1_0
R1: No; R_0603_1608Metric_Pad1.05x0.95mm_HandSolder
X1: SATA_CONNECTOR_FEM; Conn_SATA_FEM_3M_5622-2222

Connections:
+5V: J2.1, X1.P7, X1.P8, X1.P9
+12V: J2.2, J2.4, X1.P13, X1.P14, X1.P15
/HDD_Rx+: J2.5, X1.S6
/HDD_Rx-: J2.7, X1.S5
/HDD_Tx+: J2.13, X1.S2
/HDD_Tx-: J2.11, X1.S3
/SPINUP_HDD: R1.2, X1.P11
GND: J1.1, J1.2, J2.3, J2.6, J2.8, J2.9, J2.10, J2.12, J2.14, R1.1, X1.P4, X1.P5, X1.P6, X1.P10, X1.P12, X1.S1, X1.S4, X1.S7

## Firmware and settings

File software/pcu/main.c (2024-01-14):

/*
    ChibiOS - Copyright (C) 2006..2018 Giovanni Di Sirio

    Licensed under the Apache License, Version 2.0 (the "License");
    you may not use this file except in compliance with the License.
    You may obtain a copy of the License at

        http://www.apache.org/licenses/LICENSE-2.0

    Unless required by applicable law or agreed to in writing, software
    distributed under the License is distributed on an "AS IS" BASIS,
    WITHOUT WARRANTIES OR CONDITIONS OF ANY KIND, either express or implied.
    See the License for the specific language governing permissions and
    limitations under the License.
*/

#include "ch.h"
#include "hal.h"
#include "bcuCommunication.h"
#include "alarmClock.h"
#include "measurement.h"
#include "docking.h"
#include "statemachine.h"
#include "hmi/hmi.h"
#include "debug.h"

int main(void) {
    halInit();
    dockingInit();

    chSysInit();
    debug_init();
    debug_log("[I] PCU powered up\n");
    bcuCommunication_init();
    alarmClock_init();
    measurement_init();
    statemachine_init();
    hmi_init();

    while (true) {
        chThdSleepMilliseconds(1000);
    }
}

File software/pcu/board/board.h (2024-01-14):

/*
    ChibiOS - Copyright (C) 2006..2020 Giovanni Di Sirio

    Licensed under the Apache License, Version 2.0 (the "License");
    you may not use this file except in compliance with the License.
    You may obtain a copy of the License at

        http://www.apache.org/licenses/LICENSE-2.0

    Unless required by applicable law or agreed to in writing, software
    distributed under the License is distributed on an "AS IS" BASIS,
    WITHOUT WARRANTIES OR CONDITIONS OF ANY KIND, either express or implied.
    See the License for the specific language governing permissions and
    limitations under the License.
*/

/*
 * This file has been automatically generated using ChibiStudio board
 * generator plugin. Do not edit manually.
 */

#ifndef BOARD_H
#define BOARD_H

/*===========================================================================*/
/* Driver constants.                                                         */
/*===========================================================================*/

/*
 * Setup for STMicroelectronics STM32 Nucleo64-F070RB board.
 */

/*
 * Board identifier.
 */
#define BOARD_ST_NUCLEO64_F070RB
#define BOARD_NAME                  "STMicroelectronics STM32 Nucleo64-F070RB"

/*
 * Board oscillators-related settings.
 * NOTE: LSE not fitted.
 */
#if !defined(STM32_LSECLK)
#define STM32_LSECLK                0U
#endif

#define STM32_LSEDRV                (3U << 3U)

#if !defined(STM32_HSECLK)
#define STM32_HSECLK                8000000U
#endif

#define STM32_HSE_BYPASS

/*
 * MCU type as defined in the ST header.
 */
#define STM32F070xB

/*
 * IO pins assignments.
 */
#define GPIOA_ARD_A0                0U
#define GPIOA_ADC1_IN0              0U
#define GPIOA_ARD_A1                1U
#define STATOR_SUPPLY_SENSE         1U
#define GPIOA_ADC1_IN1              1U
#define GPIOA_ARD_D1                2U
#define GPIOA_USART2_TX             2U
#define GPIOA_ARD_D0                3U
#define GPIOA_USART2_RX             3U
#define GPIOA_ARD_A2                4U
#define GPIOA_ADC1_IN4              4U
#define GPIOA_LED_GREEN             5U
#define GPIOA_ARD_D12               6U
#define GPIOA_ARD_D11               7U
#define GPIOA_ARD_D7                8U

#define MOTOR_DRV2                  7U
#define MOTOR_DRV1                  8U

#define GPIOA_ARD_D8                9U
#define GPIOA_ARD_D2                10U
#define GPIOA_PIN11                 11U
#define GPIOA_PIN12                 12U
#define GPIOA_SWDIO                 13U
#define GPIOA_SWCLK                 14U
#define GPIOA_PIN15                 15U

#define HMI_PWM0_DISPLAY                0U
#define HMI_PWM1_LED                  1U
#define GPIOB_PIN2                  2U
#define nENDSWITCH_UNDOCKED         2U
#define GPIOB_SWO                   3U
#define GPIOB_ARD_D5                4U
#define GPIOB_ARD_D4                5U
#define GPIOB_ARD_D10               6U
#define GPIOB_PIN7                  7U
#define nDOCKED_SENSE2               8U
#define nDOCKED_SENSE               9U
#define HMI_USART_TX3_DISPLAY_RS        10U
#define HMI_USART_RX3_DISPLAY_E                 11U
#define HMI_NSS2_DISPLAY_DB4                 12U
#define HMI_SCK2_SCL2_DISPLAY_DB5                 13U
#define HMI_MISO2_SDA2_DISPLAY_DB6                 14U
#define HMI_MOSI2_DISPLAY_DB7                 15U
#define DEBUG_USART1_TX             6U
#define DEBUG_USART1_RX             7U

#define SW_HDD_ON                   0U
#define SW_HDD_OFF                  1U
#define SW_SBU_ON                   2U
#define SW_SBU_OFF                  3U
#define DISABLE_LM2596              4U
#define HMI_PUSHBUTTON_0                  5U
#define HMI_PUSHBUTTON_1                  6U
#define GPIOC_ARD_D9                7U
#define GPIOC_PIN8                  8U
#define GPIOC_PIN9                  9U
#define GPIOC_PIN10                 10U
#define GPIOC_PIN11                 11U
#define GPIOC_PIN12                 12U
#define GPIOC_BUTTON                13U
#define GPIOC_OSC32_IN              14U
#define GPIOC_OSC32_OUT             15U

#define GPIOD_PIN0                  0U
#define GPIOD_PIN1                  1U
#define GPIOD_PIN2                  2U
#define GPIOD_PIN3                  3U
#define GPIOD_PIN4                  4U
#define GPIOD_PIN5                  5U
#define GPIOD_PIN6                  6U
#define GPIOD_PIN7                  7U
#define GPIOD_PIN8                  8U
#define GPIOD_PIN9                  9U
#define GPIOD_PIN10                 10U
#define GPIOD_PIN11                 11U
#define GPIOD_PIN12                 12U
#define GPIOD_PIN13                 13U
#define GPIOD_PIN14                 14U
#define GPIOD_PIN15                 15U
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

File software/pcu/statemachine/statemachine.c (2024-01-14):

#include "statemachine.h"
#include "power.h"
#include "pcu_events.h"
#include "bcuCommunication.h"
#include "debug.h"

static wakeup_reason_e wakeup_reason = WAKEUP_REASON_POWER_ON;
static uint32_t milliseconds_to_shutdown = DEFAULT_MILLISECONDS_TO_SHUTDOWN;
static state_codes_e current_state = STATE_INIT;

wakeup_reason_e statemachine_getWakeupReason(void) {
    return wakeup_reason;
}

/**
 * The general architecture is that every state function is blocking and waits for events to happen.
 * It then reacts to those events and probably transitions to another state.
 */


/**
 * @return necessary to undergo the power activation process on entering active state on initial powerup
 */
int STATE_INIT_state(void) {
    return STATE_ACTIVE;
}

/**
 * @return STATE_SHUTDOWN_REQUESTED if BCU requests shutdown, otherwise STATE_ACTIVE
 */
int STATE_ACTIVE_state(void) {
    debug_log("[I] performing ACTIVE STATE action\n");
    state_codes_e next_state = STATE_ACTIVE;
    sendToBcu("active state");
    eventmask_t evt = chEvtWaitAny(ALL_EVENTS);
    if (evt & EVENT_SHUTDOWN_REQUESTED) {
        next_state = STATE_SHUTDOWN_REQUESTED;
    }
    return next_state;
}

/**
 * @brief state function for Shutdown-Requested state
 * @details runs a timer that will power off all rails
 * @return STATE_DEEP_SLEEP if shutdown timer expires, STATE_ACTIVE if BCU aborts shutdown
 */
int STATE_SHUTDOWN_REQUESTED_state(void) {
    debug_log("[I] performing SHUTDOWN REQUESTED STATE action\n");
    state_codes_e next_state = STATE_DEEP_SLEEP;
    sendToBcu("shutdown_requested state");
    eventmask_t evt = chEvtWaitAnyTimeout(ALL_EVENTS, TIME_MS2I(milliseconds_to_shutdown));
    if (evt & (EVENT_SHUTDOWN_ABORTED | EVENT_WAKEUP_REQUESTED_BY_ALARMCLOCK )) {
        next_state = STATE_ACTIVE;
    }
    return next_state;
}

/**
 * @return
 */
int STATE_DEEP_SLEEP_state(void) {
    debug_log("[I] performing DEEP SLEEP STATE action\n");
    state_codes_e next_state = STATE_DEEP_SLEEP;
    sendToBcu("deep_sleep state");
    eventmask_t evt = chEvtWaitAny(ALL_EVENTS);
    if (evt & EVENT_WAKEUP_REQUESTED_BY_ALARMCLOCK) {
        wakeup_reason = WAKEUP_REASON_SCHEDULED;
        next_state = STATE_ACTIVE;
    }
    else if (evt & EVENT_WAKEUP_REQUESTED_BY_USER) {
        wakeup_reason = WAKEUP_REASON_USER_REQUEST;
        next_state = STATE_ACTIVE;
    }
    else if (evt & (EVENT_BUTTON_0_PRESSED | EVENT_BUTTON_1_PRESSED)) {
        next_state = STATE_HMI;
    }
    return next_state;
}

int STATE_HMI_state(void) {
    debug_log("[I] performing HMI STATE action\n");
    state_codes_e next_state = STATE_DEEP_SLEEP;
    sendToBcu("hmi state");
    eventmask_t evt = chEvtWaitAnyTimeout(ALL_EVENTS, TIME_MS2I(60000));
    if (evt & EVENT_WAKEUP_REQUESTED_BY_ALARMCLOCK) {
        wakeup_reason = WAKEUP_REASON_SCHEDULED;
        next_state = STATE_ACTIVE;
    }
    else if (evt & EVENT_BUTTON_0_PRESSED) {
        sendToBcu("Button 0 pressed");
    }
    else if (evt & EVENT_BUTTON_1_PRESSED) {
        sendToBcu("Button 1 pressed");
    }
    else if (evt & EVENT_WAKEUP_REQUESTED_BY_USER) {
        wakeup_reason = WAKEUP_REASON_USER_REQUEST;
        next_state = STATE_ACTIVE;
    }
    return next_state;
}

/* array and enum must be in sync! */
int (* state[])(void) = {
    STATE_INIT_state,
    STATE_ACTIVE_state,
    STATE_SHUTDOWN_REQUESTED_state,
    STATE_DEEP_SLEEP_state,
    STATE_HMI_state
};

struct transition {
    state_codes_e src_state;
    state_codes_e dst_state;
};

struct transition state_transitions[] = {
        {STATE_INIT, STATE_ACTIVE},
        {STATE_ACTIVE, STATE_SHUTDOWN_REQUESTED},
        {STATE_SHUTDOWN_REQUESTED,   STATE_ACTIVE},
        {STATE_SHUTDOWN_REQUESTED,   STATE_DEEP_SLEEP},
        {STATE_DEEP_SLEEP,   STATE_ACTIVE},
        {STATE_DEEP_SLEEP,   STATE_HMI},
        {STATE_HMI,   STATE_DEEP_SLEEP},
        {STATE_HMI,   STATE_ACTIVE}
};

#define EXIT_STATE STATE_DEEP_SLEEP

#define DIMENSION(x) (uint8_t)(sizeof(x)/sizeof(x[0]))

bool transition_valid(state_codes_e cur_state, state_codes_e desired_state) {
    for (uint8_t i = 0; i < DIMENSION(state_transitions); i++) {
        if (state_transitions[i].src_state == cur_state && state_transitions[i].dst_state == desired_state) {
            return true;
        }
    }
    return false;
}

/**
 * @brief transitions to the next state. If a transition is valid, it moreover conducts actions that need to be done
 * at state leaving and state entry respectively
 * @param desired_state
 * @return current state AFTER function was called. Is the current state in case the transition is invalid
 */
state_codes_e statemachine_transitionToState(state_codes_e current_state, state_codes_e desired_state) {
    if (!transition_valid(current_state, desired_state)) {
        debug_log("[W] statemachine transitioning from %d to %d is INVALID\n", current_state, desired_state);
        return current_state;
    }
    debug_log("[I] statemachine transitioning from %d to %d\n", current_state, desired_state);

    /* perform actions on leaving a state */
    switch (current_state) {
        case STATE_DEEP_SLEEP:
            power5v();
            break;
        default:
            break;
    }

    /* perform actions on entering a state */
    switch (desired_state) {
        case STATE_DEEP_SLEEP:
            unpowerBcu();
            unpower5v();
            break;

        case STATE_ACTIVE:
            powerBcu();
            break;

        default:
            break;
    }
    return desired_state;
}

/**
 * @brief statemachine entry point
 */
void statemachine_mainloop(void) {
    int (* state_fun)(void);
    state_codes_e desired_state = STATE_ACTIVE;

    power5v();  // necessary to turn it on initially

    while(true) {
        state_fun = state[current_state];
        desired_state = state_fun();
        if (desired_state != current_state) {
            current_state = statemachine_transitionToState(current_state, desired_state);
        }
        chThdSleepMilliseconds(100);
    }
}

thread_t *uart_thread;

static THD_WORKING_AREA(waUARTThread, 1024);
static THD_FUNCTION(UARTThread, arg) {
    UNUSED_PARAM(arg);
    while (true) {
        statemachine_mainloop();
    }
}

void statemachine_init(void) {
    uart_thread = chThdCreateStatic(waUARTThread, sizeof(waUARTThread),
                                    NORMALPRIO + 1, UARTThread, NULL);
}

void statemachine_sendEvent(eventmask_t events) {
    chEvtSignal(uart_thread, events);
}

void statemachine_sendEventFromIsr(eventmask_t events) {
    chSysLockFromISR();
    chEvtSignalI(uart_thread, events);
    chSysUnlockFromISR();
}

void statemachine_setMillisecondsToShutdown(uint32_t milliseconds) {
    milliseconds_to_shutdown = milliseconds;
}

state_codes_e statemachine_getCurrentState(void) {
    return current_state;
}

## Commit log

2024-01-04 [HW] add power pcb
2024-01-04 [HW] add hmi circuit board
2024-01-04 [HW] add sata adapter pcbs
2024-01-04 [HW] add 3d printing parts
    [BaSe_Auflager_Platinen_rev4.stl, BaSe_BP_HDD_rev1.stl, BaSe_Bodenplatte_rev3.stl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]
2024-01-04 [HW] add rev3a BOM
    [BaSe_rev3a_Stueckliste_V1_0.ods]
2024-01-04 [HW] add rev3b BOM
    [BaSe_rev3a_Stueckliste_V1_0.ods, BaSe_rev3b_Stueckliste_V1_0.ods]
2024-01-04 [HW] add 3d printing parts explosion drawings
2024-01-04 [Orga] cleanup
    [BaSe_Auflager_Platinen_rev4.stl, BaSe_BP_HDD_rev1.stl, BaSe_Bodenplatte_rev3.stl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]
2024-01-04 [PCU] create board-files
2024-01-04 [PCU] introduce measurement for adc
2024-01-04 [PCU] relay control implemented
2024-01-04 [PCU] implement 5v control
2024-01-04 [HW] second version, never built up. First version has no kicad files, just hand-sketches
    [Additional_Outputs.kicad_sch, BackupServer.kicad_sch, Motor_Driver.kicad_sch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]
2024-01-04 [HW] v2.0, made of the blue breadboard
    [Additional_Outputs.kicad_sch, BackupServer.kicad_sch, Motor_Driver.kicad_sch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]
2024-01-04 [HW] v3 with raspberry pi 4
    [BaSe_PWR_V3_1.kicad_pcb, BaSe_PWR_V3_1.kicad_sch, BackupServer.kicad_sch]
2024-01-04 [HW] new base pwr version
    [BaSe_PWR_V3_2.kicad_pcb, BaSe_PWR_V3_2.kicad_sch]
2024-01-04 [HW] first hmi board version
    [BaSe_HMI_V1_0.kicad_pcb, BaSe_HMI_V1_0.kicad_sch, BaSe_PWR_V3_1.kicad_pcb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]
2024-01-04 [HW] first version of sata adapter boards
    [BaSe_SATA_Adapter_Carriage_V1_0.kicad_pcb, BaSe_SATA_Adapter_Carriage_V1_0.kicad_sch, BaSe_SATA_Adapter_HDD_V1_0.kicad_pcb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]
2024-01-04 [HW] production ready versions of sata adapter boards
    [BaSe_SATA_Adapter_Carriage_V1_0.kicad_pcb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]
2024-01-04 [HW] production ready version of base pwr
    [BaSe_PWR_V3_2-B_Mask.gbr, BaSe_PWR_V3_2-B_Paste.gbr, BaSe_PWR_V3_2-Edge_Cuts.gbr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]
2024-01-04 [HW] production ready version of base hmi
    [BaSe_HMI_V1_0.kicad_pcb, BaSe_HMI_V1_0.kicad_sch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]
2024-01-04 [HW] add 3d printing parts (stl files)
    [BaSe_Auflager_Platinen_rev4.stl, BaSe_BP_HDD_rev1.stl, BaSe_Bodenplatte_rev3.stl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]
2024-01-04 [HW] add bill of materials
    [BaSe_rev3a_Stueckliste_V1_0.ods, BaSe_rev3b_Stueckliste_V1_0.ods]
2024-01-04 [HW] testboard for the motor driver and current measurement
    [BaSe_DC_Motor_Test_V1_0-B_Cu.gbr, BaSe_DC_Motor_Test_V1_0-B_Mask.gbr, BaSe_DC_Motor_Test_V1_0-B_Paste.gbr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]
2024-01-04 [HW] test pcb for the dockable usb connection
    [BaSe_SATA_Adapter_Carriage_V1_1-B_Cu.gbr, BaSe_SATA_Adapter_Carriage_V1_1-B_Mask.gbr, BaSe_SATA_Adapter_Carriage_V1_1-B_Paste.gbr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]
2024-01-04 [HW] BaSe_PWR_V4_0: create PCBs
    [BaSe_PWR_V3_2-B_Mask.gbr, BaSe_PWR_V3_2-B_Paste.gbr, BaSe_PWR_V3_2-Edge_Cuts.gbr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]
2024-01-04 [HW] add hardware
    [BaSe_Auflager_Platinen_rev4.stl, BaSe_BP_HDD_rev1.stl, BaSe_Bodenplatte_rev3.stl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]
2024-01-28 [HW] add hw rev4 3d printing parts
    [BaSe_Auflager_Platinen_rev4.stl, BaSe_BP_HDD_rev1.stl, BaSe_Bodenplatte_rev3.stl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]
